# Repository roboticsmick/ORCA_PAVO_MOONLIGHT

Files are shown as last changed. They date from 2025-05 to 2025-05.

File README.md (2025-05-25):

# BetaFPV Pavo20 Pro + CaddxFPV Walksnail Moonlight 4K FPV Frame

A custom FPV frame designed for the BetaFPV Pavo20 Pro frame with the CaddxFPV Walksnail Moonlight Kit digital 4K/60fps camera system at 25 degrees.

Screenshot from 2025-05-25 16-22-57
Screenshot from 2025-05-25 15-37-20
Screenshot from 2025-05-25 16-32-25

It also has cable management for the two antennas, and a mounting slot for the FlyFishRC M10 Mini GPS Module.

Screenshot from 2025-05-25 16-23-04
Screenshot from 2025-05-25 15-40-12
Screenshot from 2025-05-25 16-01-24

## 3D Printing Manufacturing

🔗 **(Pending approval from JLC) Order directly from JLC:** [JLC3DP FPV Frame](https://jlc3dp.com/3d-models/detail/MX11062-BetaFPV-Pavo20-Pro-Whoop-+-CaddxFPV-Walksnail-Moonlight-4K-FPV-Frame)]

### Printing setup
- 3D Technology: MJF(Nylon)
- Material: PA12-HP Nylon
- Surface Finish: Dyeing-Dyed Black
- Estimated Build Time: 72 hours
- Product Category: Plastic Enclosure
- Cost: ~$7 (Frame $5 + Mount $2)

Screenshot from 2025-05-25 16-32-36

## Additional parts

- 4 x M2 x 3mm - Mounting the Moonlight VTX mount
- 4 x M2 x 5mm - Mounting the Moonlight Camera mount
- 4 x M2 x 12mm - Mounting the Pavo20 Shroud mount
- 4 x M2 Locking Nuts with Nylon Inserts - Mounting the Pavo20 Shroud mount
- 4 x M2 Nylon washers - Mounting the Pavo20 Shroud mount
- 1 x M2 Spiral Straight Groove Thread Tap - Tapping the FPV frame
- 1 x 1.5mm Drill bit - Pre-drill the FPV frame
- 1 x FlyFishRC M10 Mini GPS Module

Screenshot from 2025-05-25 15-00-39

## Installation

1. Tap the mounting brackets using an M2 tap. I predrilled these with a 1.5mm drill just to clean out the holes.
2. Install FlyFishRC M10 Mini GPS Module and hold in place with some hot glue (might add a M2 bolted bracket for this at a later date). There are instructions for wiring this on youtube. Just a warning note, the original wire harness that comes with the GPS melted from touching the VTX. I replaced it with some better silicone wire to prevent future shorts. Be careful.
3. I replaced the bolts connecting the frame to the shroud with M2 12MM bolts and added a M2 nylon locking nut, and washer before the grommet. This prevented the bolt from coming undone due to vibrations. 

Screenshot from 2025-05-25 15-40-21

## Sharing is caring :helicopter:

Use as you like for your personal use. If you're rich, feel free to buy me a coffee or a HOTA 4-channel battery charger ❤️

<a href="https://www.buymeacoffee.com/orcamick" target="_blank">Buy Me A Coffee</a>

## Licensed: CC BY-NC-SA 4.0

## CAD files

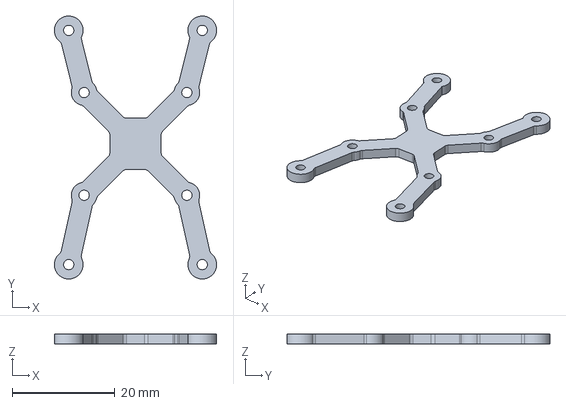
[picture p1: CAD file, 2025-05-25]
PAVO20_PRO_MOONLIGHT_BASE_2MM.step
31.6 x 51.2 x 2.00 mm

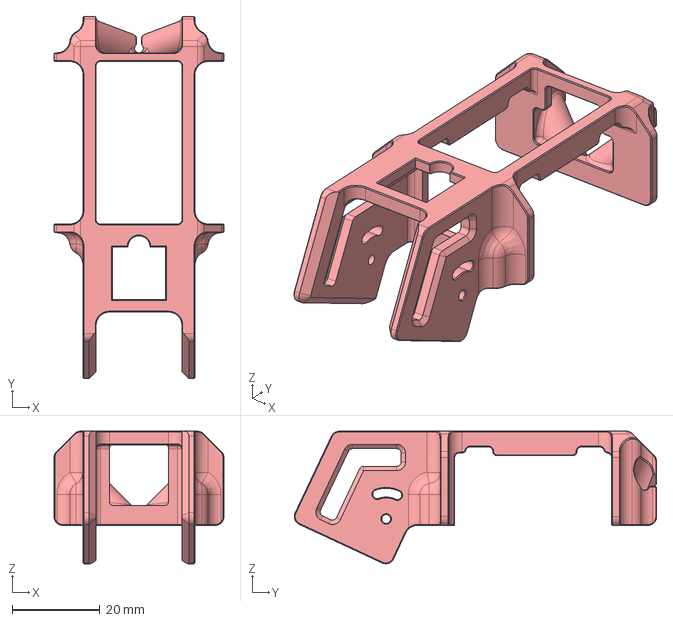
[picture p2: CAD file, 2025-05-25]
PAVO20_PRO_MOONLIGHT_FRAME.step
38.8 x 82.7 x 30.3 mm
